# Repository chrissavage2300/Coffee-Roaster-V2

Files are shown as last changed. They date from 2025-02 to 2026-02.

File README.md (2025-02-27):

# Coffee-Roaster-V2
My Second DIY coffee roaster

Parts not listed on BOM:

Intake fan: BL4447-04W-B49

https://www.aliexpress.us/item/2251800670595894.html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

Exhaust fan: 4090D 12V

https://www.aliexpress.us/item/3256805403626998.html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

SSR: GSR1-1-25DA

https://www.aliexpress.us/item/3256802111187964.html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

Gears for drum: 1M40T-Bore 6 mm

https://www.aliexpress.us/item/2255800052157775.html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

Drum Motor: 12V Single Motor, 66RPM

https://www.aliexpress.us/item/3256805242242724.html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

K type thermocouples:

https://finglai.aliexpress.com/store/1100819105?spm=a2g0o.order_list.order_list_main.187.4b841802Pr1vyz

Knobs:

https://www.aliexpress.us/item/3256807011356288.html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

LCD

https://www.aliexpress.us/item/2251832723901253.html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

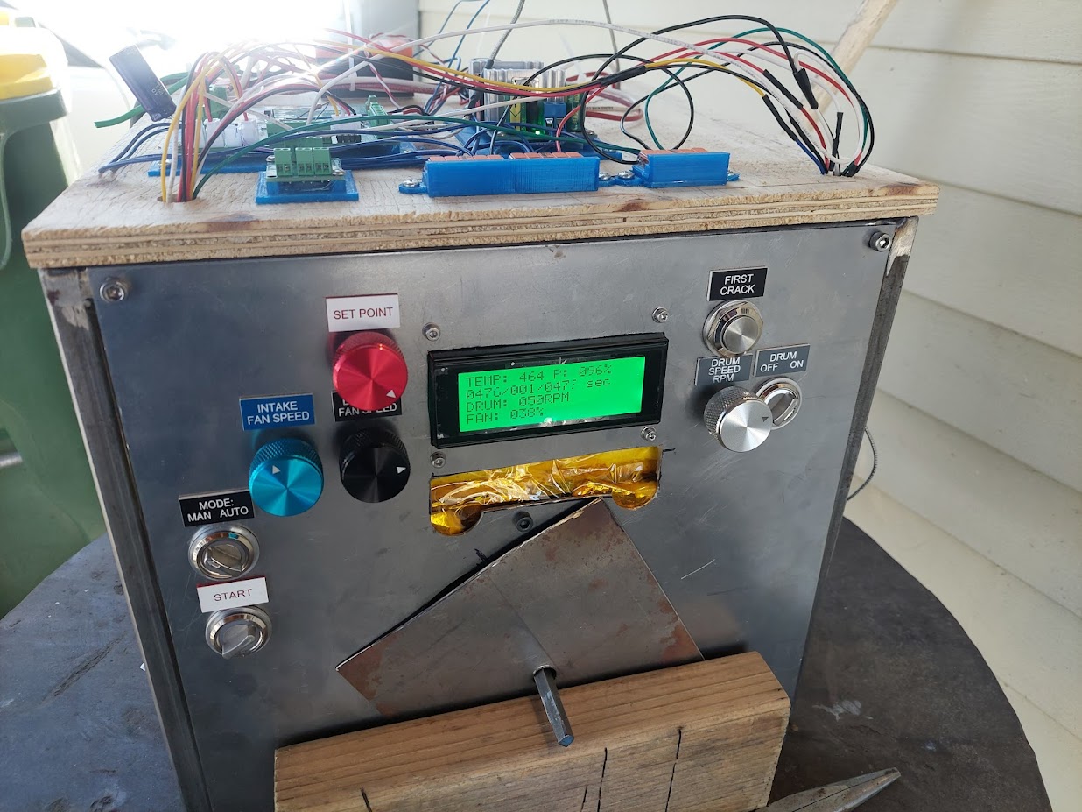
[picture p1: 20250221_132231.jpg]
roaster


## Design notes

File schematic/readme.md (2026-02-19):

I used Eagle PCB. I will convert further versions to KiCad

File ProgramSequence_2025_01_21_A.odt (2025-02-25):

Two Modes of operation via a selector switch that toggles each mode:
Green is to do

Manual Mode: □

- Set Point Pot will set the amount of power from 0 to 100%□
- in code this will be 0 to 31000 increments that determine how much power gets passed to the heater. This turns the auto mode off. This mode uses Output compare module #3□
- There will be an over temp set in the program of 470 degrees. This is for the feedback temperature, not the set point.
- Over temp condition will shut off the heater. Start LED will blink.
- ~~A Blue LED will come on~~ No LED

Auto mode (not implemented) □

- Will perform a PI function to control the heater based on the set point set via a pot.
- PI code will adjust heater until its up to temp. This turns off manual mode.
- A Blue LED will come on.

In both modes:

Intake and exhaust fans are DC PWM control and come in when start button is on. Exhaust fan not implemented yet.

- Display 0-100%□
- Fans will be OFF when start button is OFF. □
- Start LED will come on□

Drum Speed has on and off latched switch

- Display 0 to 66 RPM (0 to 100% Duty) □

Start mode is a latched switch. This starts either mode. Switching it off will stop the machine ~~and reset any counters~~

-Addendum: Timer can be reset with start mode off and FC pressed. □

First Crack push button sets the current time to 0 and displays the time at which the button was pressed. □

- 1 second timer counts up until user hits FC button. This will use the INT0 interrupt pin to count up to 120, which is one second. We use the INT0 pin because line frequency might be more accurate. □
- NOTE: FRC is accurate to +/-3%. 1 Second time means 1.03 to 0.98 seconds. Over 10 minutes this is +/-18 seconds.
- Screen will be updated during this time. □
- I2C ADC will also be read during this time □

ADC algorithm will perform calculation on K-type thermocouple using linearization based on voltage.

Formula for final thermocouple is as follows: first the MCP9800 must be read, this gives the temperature in a digital format. Then the temperature must be converted back into a voltage via a linear formula. The onboard temp sensor should only see temperatures up to 40C, so the formula only goes up this far. I’ll call this VCJC, or Voltage Cold Junction Comp. □

Then the thermocouple voltage will be read. This voltage, called Vtc (thermocouple voltage) will then be added to Vcjc. The final voltage will be entered into an equation to solve for the temperature.

□20 Minute Burn in test without heat

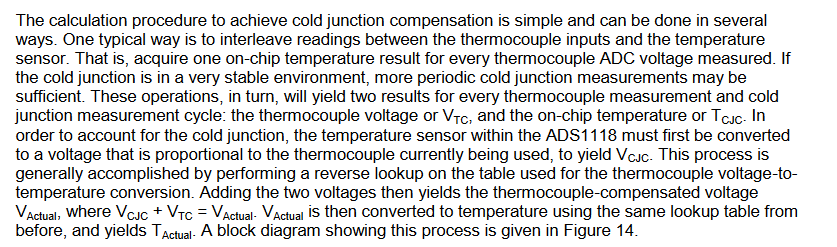
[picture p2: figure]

□20 minute burn in test with heat

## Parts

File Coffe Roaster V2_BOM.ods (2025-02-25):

Part | Value | Device | Package | Description
12V | M025MM | M025MM | SCREWTERMINAL-5MM-2 | Standard 2-pin 0.1" header. Use with
120VACOUT | M025MM | M025MM | SCREWTERMINAL-5MM-2 | Standard 2-pin 0.1" header. Use with
C1 | 0.1uF | CAP0805 | 805 | Capacitor
C2 | 0.1uF | CAP0805 | 805 | Capacitor
C3 | 0.1uF | CAP0805 | 805 | Capacitor
C4 | 0.1uF | CAP0805 | 805 | Capacitor
C5 | 0.1u | CAP1206 | 1206 | Capacitor
C6 | 0.1u | CAP1206 | 1206 | Capacitor
C7 | 0.1u | CAP1206 | 1206 | Capacitor
C8 | 0.1uF | CAP0805 | 805 | Capacitor
C9 | 0.1uF | CAP0805 | 805 | Capacitor
C10 | 0.1uF | CAP0805 | 805 | Capacitor
C11 | 0.1uF | CAP0805 | 805 | Capacitor
C12 | 0.1uF | CAP0805 | 805 | Capacitor
C13 | 0.1uF | CAP0805 | 805 | Capacitor
DRUM |  | M03POLAR_LOCK | MOLEX-1X3_LOCK | Header 3
EXT |  | M03POLAR_LOCK | MOLEX-1X3_LOCK | Header 3
F1 | 16A | FUSE | FUSE | FUSE
FAN | M02POLAR_LOCK | M02POLAR_LOCK | MOLEX-1X2_LOCK | Standard 2-pin 0.1" header. Use with
I2C2 | I2C5V | M04JST | 1X04-1.5MM_JST | Header 4
IC1 | AZ1117C | ADP3338AKCZ-5-R7 | SOT230P700X180-4N | Low Dropout Regulator
IC2 | AZ1117CR-3.3TRG1 | AZ1117CR-3.3TRG1 | SOT89_AZ1117_DIO
IC4 | MCP9801-M/SNSOIC8-N_MC_MCH-M | MCP9801-M/SNSOIC8-N_MC_MCH-M | SOIC8-N_MC_MCH-M
IC5 | MCP3424-E/SLSOIC14-N_MC_MCH-M | MCP3424-E/SLSOIC14-N_MC_MCH-M | SOIC14-N_MC_MCH-M | Analog to Digital Converters - ADC 18B delta-sigma ADC dual Ch 4sps
INT |  | M03POLAR_LOCK | MOLEX-1X3_LOCK | Header 3
ISO1 | MOC3021SMOC3021S_LTO-M | MOC3021SMOC3021S_LTO-M | MOC3021S_LTO-M
ISO2 | LTV-814S-TA1 | SFH6206 | DIL4-SMD | Optocoupler, Phototransistor Output, AC Input
J2 | EXPANSION | M04JST | 1X04-1.5MM_JST | Header 4
JP1 | ICSP | M05PTH | 1X05 | Header 5
JP2 |  | M02POLAR_LOCK | MOLEX-1X2_LOCK | Header 2
JP3 |  | M02POLAR_LOCK | MOLEX-1X2_LOCK | Header 2
JP4 | M01PTH | M01PTH | 1X01 | Header 1
JP5 | UART | M04LOCK | 1X04_LOCK | Header 4
JP6 |  | M083.5MM-8 | SCREWTERMINAL-3.5MM-8 | Header 8
JP7 |  | M02POLAR_LOCK | MOLEX-1X2_LOCK | Header 2
JP8 |  | M04LOCK_LONGPADS | 1X04_LOCK_LONGPADS | Header 4
JP10 | M10LOCK_LONGPADS | M10LOCK_LONGPADS | 1X10_LOCK_LONGPADS | Header 10
JP11 | M01PTH | M01PTH | 1X01 | Header 1
LED1 | GRN | LED1206 | LED-1206 | LEDs
LED2 | YELLOW | LED1206 | LED-1206 | LEDs
LED3 | GRN | LED1206 | LED-1206 | LEDs
LED4 | YELLOW | LED1206 | LED-1206 | LEDs
LED5 | BLUE | LED1206 | LED-1206 | LEDs
LED6 | BLUE | LED1206 | LED-1206 | LEDs
PIN | M025MM | M025MM | SCREWTERMINAL-5MM-2 | Standard 2-pin 0.1" header. Use with
POUT | M025MM | M025MM | SCREWTERMINAL-5MM-2 | Standard 2-pin 0.1" header. Use with
Q1 | DMN3032LE-13 | NFET_SOT_223 | SOT223
Q2 | DMN3032LE-13 | NFET_SOT_223 | SOT223
Q3 | DMN3032LE-13 | NFET_SOT_223 | SOT223
R1 | 200 | R-US_R2512 | R2512 | RESISTOR, American symbol
R2 | 15k | R-US_R2512 | R2512 | RESISTOR, American symbol
R3 | 15k | R-US_R2512 | R2512 | RESISTOR, American symbol
R4 | 220 | RESISTOR1206 | 1206 | Resistor
R5 | 2k | RESISTOR1206 | 1206 | Resistor
R6 | 340 | RESISTOR1206 | 1206 | Resistor
R7 | 2k | RESISTOR1206 | 1206 | Resistor
R8 | 10k | R-US_M0805 | M0805 | RESISTOR, American symbol
R9 | 10k | R-US_M0805 | M0805 | RESISTOR, American symbol
R10 | 340 | RESISTOR1206 | 1206 | Resistor
R11 | 2k | RESISTOR1206 | 1206 | Resistor
R12 | 2k | RESISTOR1206 | 1206 | Resistor
R15 | 2k | RESISTOR1206 | 1206 | Resistor
R16 | 2k | RESISTOR1206 | 1206 | Resistor
R19 | 340 | RESISTOR1206 | 1206 | Resistor
R20 | 100k | RESISTOR1206 | 1206 | Resistor
SP |  | M03POLAR_LOCK | MOLEX-1X3_LOCK | Header 3
T1 | BT138-600,127 | BT138-V | TO220BV | TRIAC
U2 | DSPIC33EP32MC204-I/PTTQFP44_10X10MC_MCH-M | DSPIC33EP32MC204-I/PTTQFP44_10X10MC_MCH-M | TQFP44_10X10MC_MCH-M

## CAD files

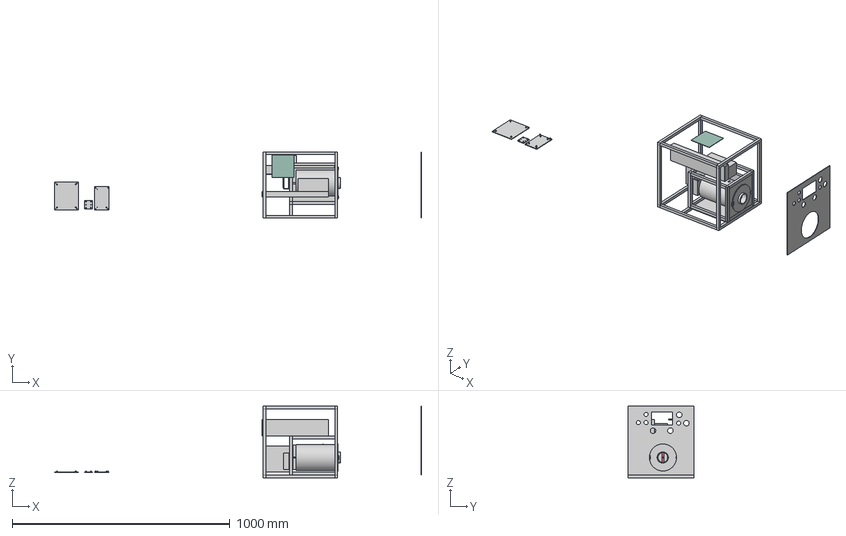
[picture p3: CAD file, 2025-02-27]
3D CAD/Coffee Roaster V2.0 v107.step
1686.0 x 304.8 x 330.2 mm
Make This Part (1)
Drum (1)
End Cap (Cut) (1)
1800W Heater
FAN (1)
bushing2
Motor Holder
FL
FrontLeft (1)
BL
TL
1603A2_Surface-Mount Hinge with Holes
4x4PCB

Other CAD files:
3D CAD/Coffee Roaster V2.0 v107.f3d

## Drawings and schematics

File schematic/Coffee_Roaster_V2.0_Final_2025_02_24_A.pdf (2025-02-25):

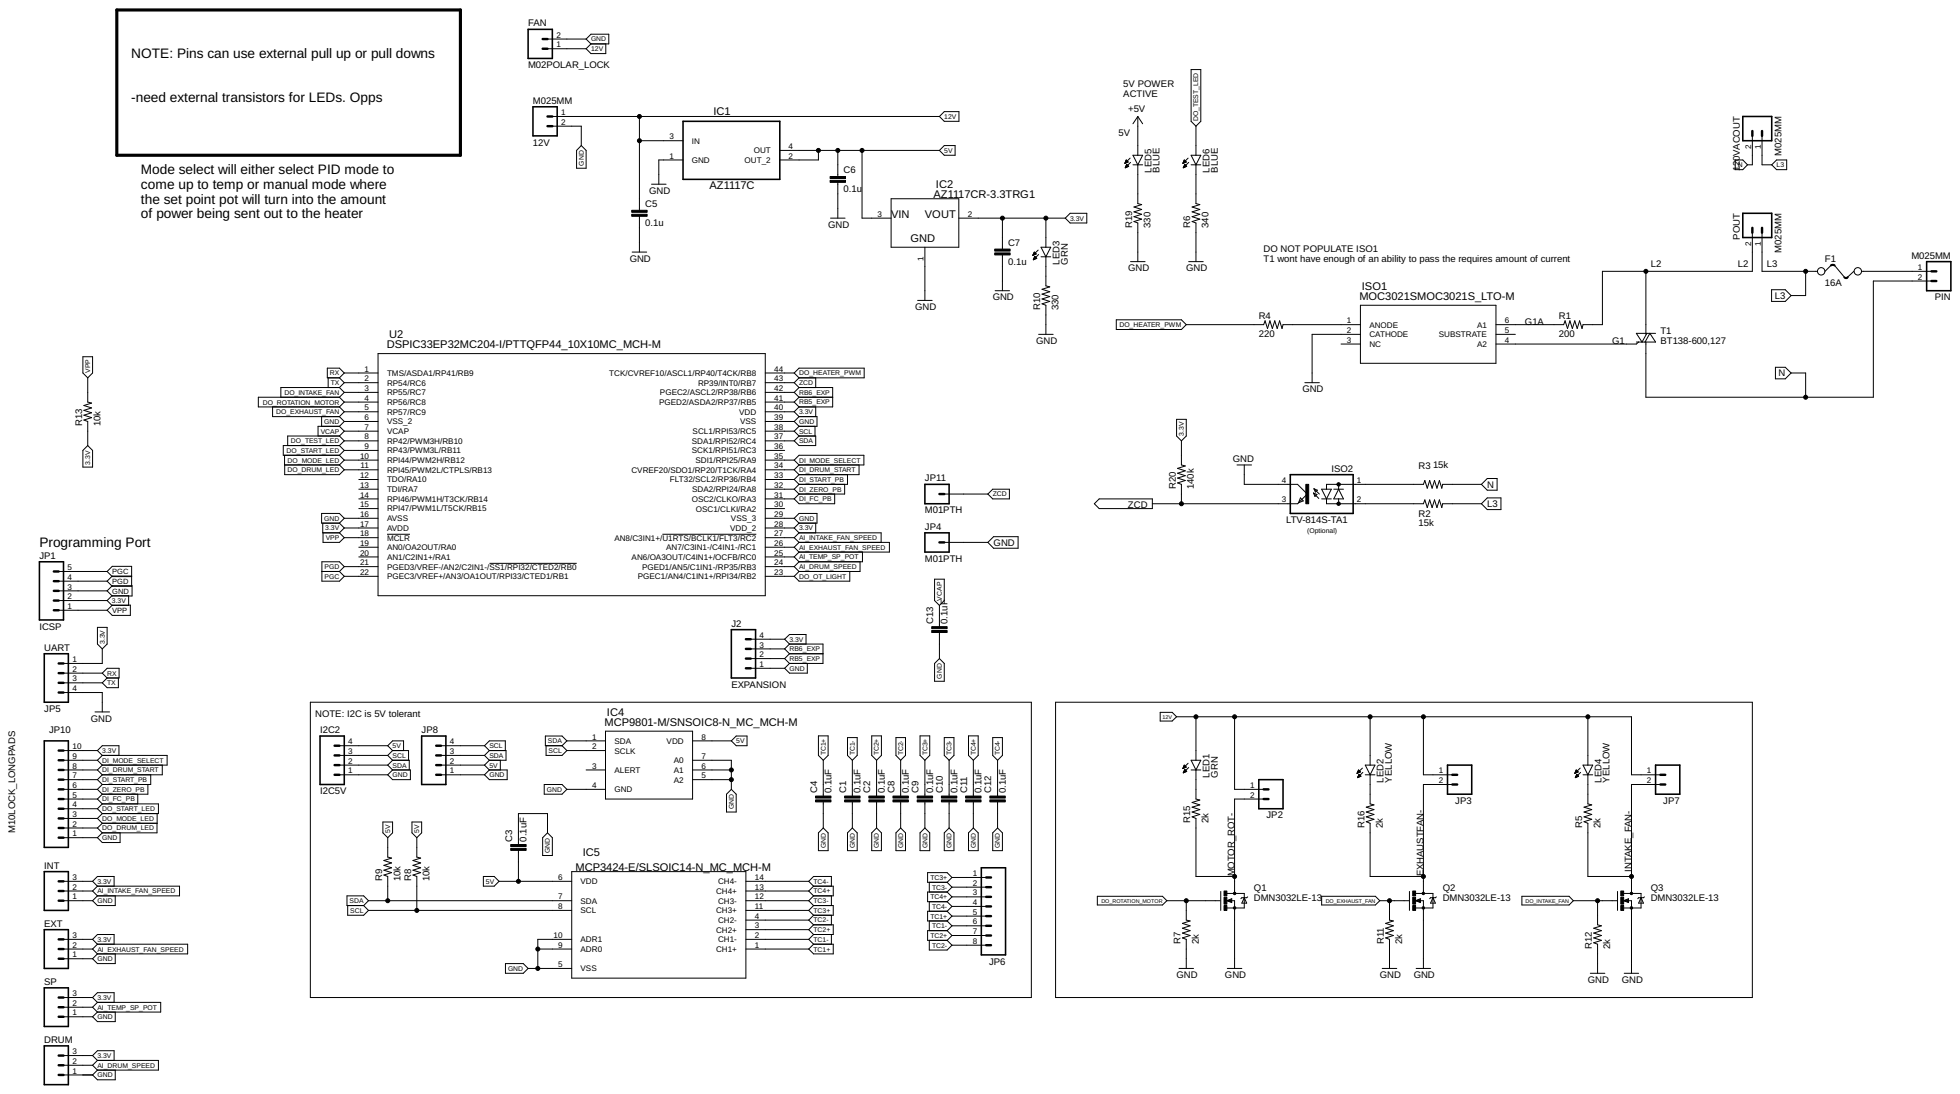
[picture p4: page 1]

ACTIVE NOTE: Pins can use external pull up or pull downs

-need external transistors for LEDs. Opps Mode select will either select PID mode to

come up to temp or manual mode where

GND GND GND GND

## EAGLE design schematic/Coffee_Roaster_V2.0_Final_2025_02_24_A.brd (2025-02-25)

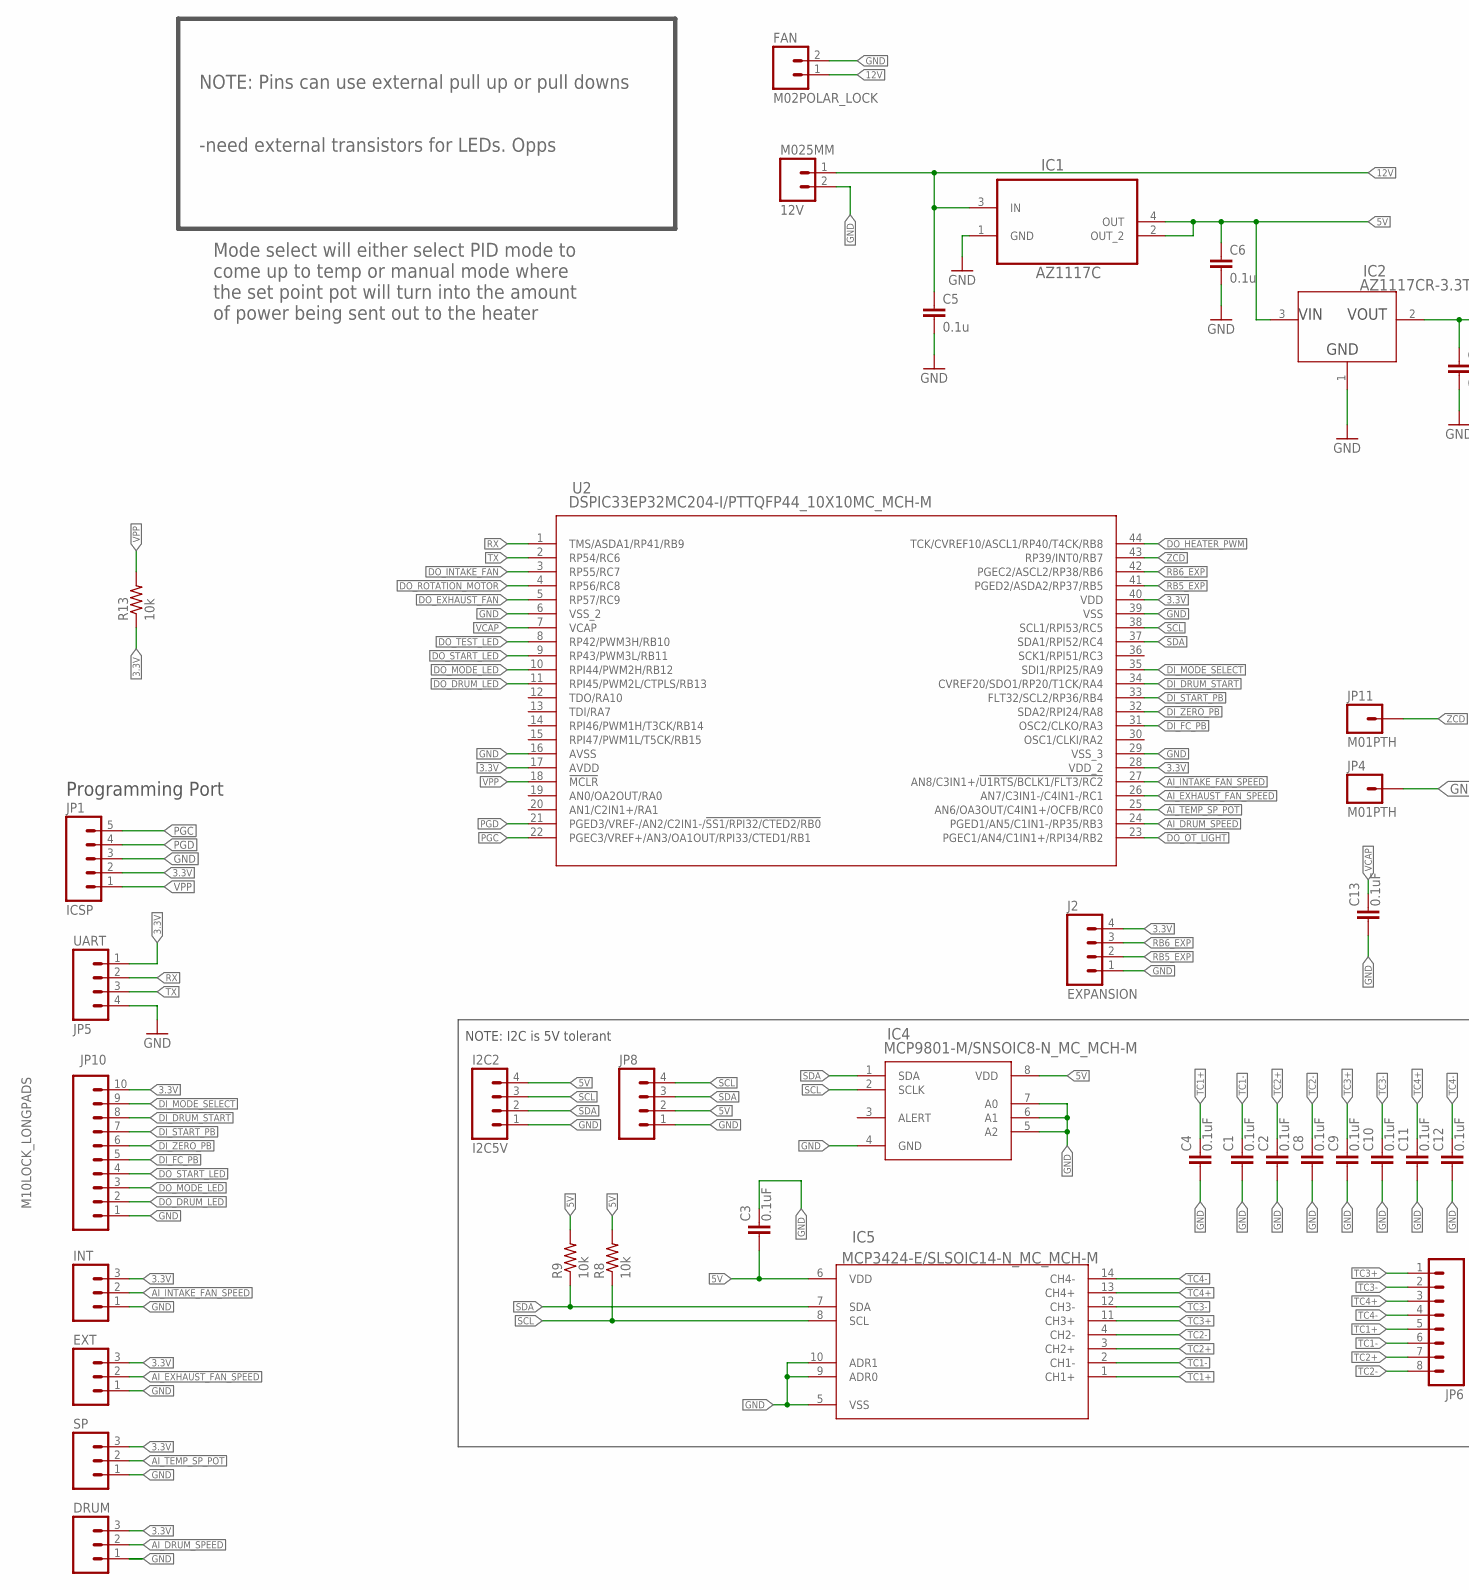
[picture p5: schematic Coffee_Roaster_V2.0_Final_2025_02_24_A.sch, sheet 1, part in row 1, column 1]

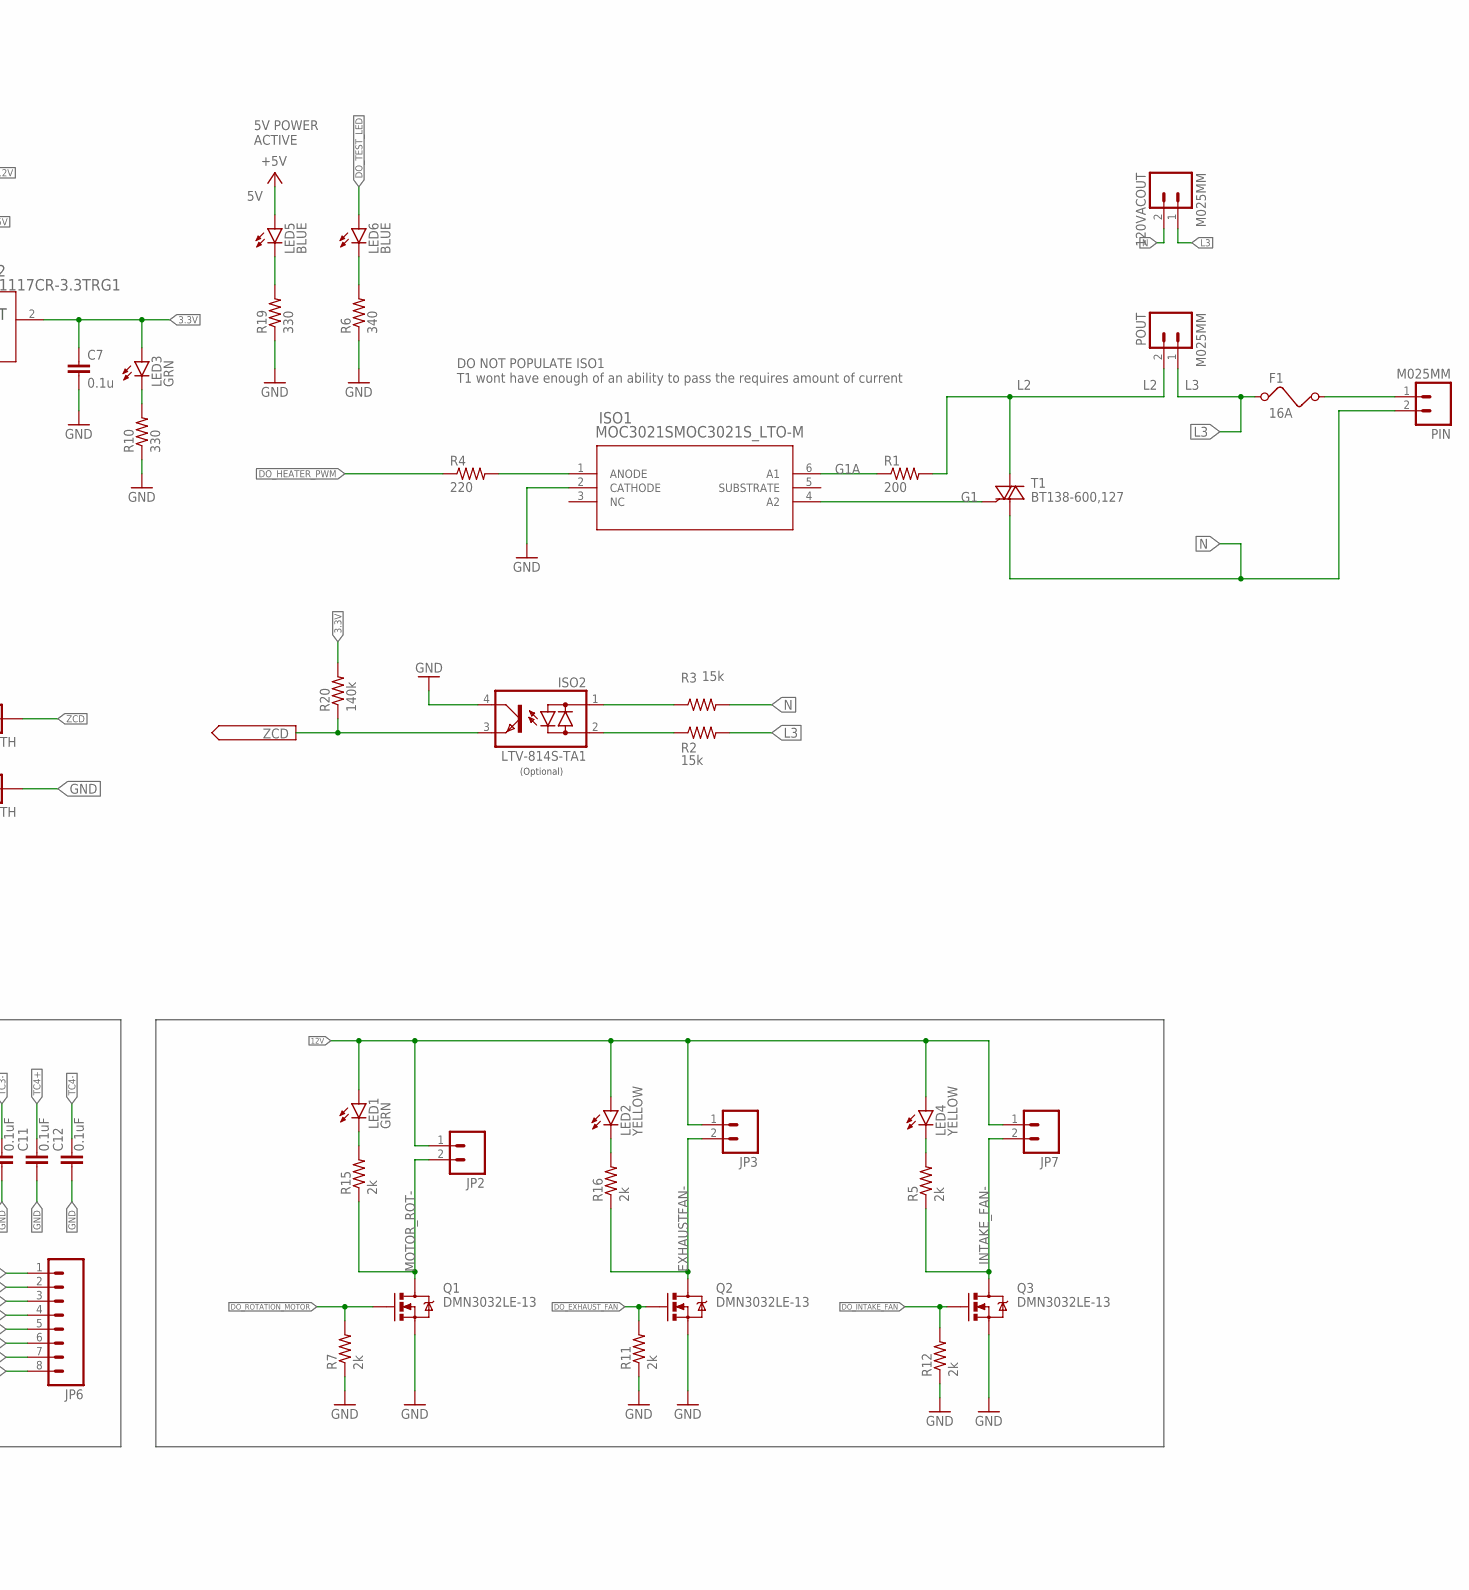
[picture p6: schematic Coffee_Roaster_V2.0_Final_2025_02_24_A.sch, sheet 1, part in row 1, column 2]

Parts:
12V, 120VACOUT: M025MM; SCREWTERMINAL-5MM-2
C1, C2, C3, C4, C8, C9, C10, C11, C12, C13: 0.1uF; 0805
C5, C6, C7: 0.1u; 1206
DRUM: M03POLAR_LOCK; MOLEX-1X3_LOCK
EXT: M03POLAR_LOCK; MOLEX-1X3_LOCK
F1: 16A; FUSE
FAN: M02POLAR_LOCK; MOLEX-1X2_LOCK
I2C2: I2C5V; 1X04-1.5MM_JST
IC1: AZ1117C; SOT230P700X180-4N
IC2: AZ1117CR-3.3TRG1; SOT89_AZ1117_DIO
IC4: MCP9801-M/SNSOIC8-N_MC_MCH-M; SOIC8-N_MC_MCH-M
IC5: MCP3424-E/SLSOIC14-N_MC_MCH-M; SOIC14-N_MC_MCH-M
INT: M03POLAR_LOCK; MOLEX-1X3_LOCK
ISO1: MOC3021SMOC3021S_LTO-M; MOC3021S_LTO-M
ISO2: LTV-814S-TA1; DIL4-SMD
J2: EXPANSION; 1X04-1.5MM_JST
JP1: ICSP; 1X05
JP2, JP3, JP7: M02POLAR_LOCK; MOLEX-1X2_LOCK
JP4, JP11: M01PTH; 1X01
JP5: UART; 1X04_LOCK
JP6: M083.5MM-8; SCREWTERMINAL-3.5MM-8
JP8: M04LOCK_LONGPADS; 1X04_LOCK_LONGPADS
JP10: M10LOCK_LONGPADS; 1X10_LOCK_LONGPADS
LED1, LED3: GRN; LED-1206
LED2, LED4: YELLOW; LED-1206
LED5, LED6: BLUE; LED-1206
PIN: M025MM; SCREWTERMINAL-5MM-2
POUT: M025MM; SCREWTERMINAL-5MM-2
Q1, Q2, Q3: DMN3032LE-13; SOT223
R1: 200; R2512
R2, R3: 15k; R2512
R4: 220; 1206
R5, R7, R11, R12, R15, R16: 2k; 1206
R6: 340; 1206
R8, R9, R13: 10k; M0805
R10, R19: 330; 1206
R20: 140k; 1206
SP: M03POLAR_LOCK; MOLEX-1X3_LOCK
T1: BT138-600,127; TO220BV
U2: DSPIC33EP32MC204-I/PTTQFP44_10X10MC_MCH-M; TQFP44_10X10MC_MCH-M

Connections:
3.3V: C7.1, DRUM.3, EXT.3, IC2.2 (OUTPUT), INT.3, J2.4, JP1.2, JP5.1, JP10.10, LED3.A, R13.1, R20.2, SP.3, U2.17 (AVDD), U2.28 (VDD_2), U2.40 (VDD)
5V: C3.1, C6.1, I2C2.4, IC1.2 (OUT_2), IC1.4 (OUT), IC2.3 (INPUT), IC4.8 (VDD), IC5.6 (VDD), JP8.2, LED5.A, R8.2, R9.2
12V: 12V.1, C5.1, FAN.1, IC1.3 (IN), JP2.1, JP3.1, JP7.1, LED1.A, LED2.A, LED4.A
AI_DRUM_SPEED: DRUM.2, U2.24 (PGED1/AN5/C1IN1-/RP35/RB3)
AI_EXHAUST_FAN_SPEED: EXT.2, U2.26 (AN7/C3IN1-/C4IN1-/RC1)
AI_INTAKE_FAN_SPEED: INT.2, U2.27 (AN8/C3IN1+/!U1RTS/BCLK1/FLT3/RC2)
AI_TEMP_SP_POT: SP.2, U2.25 (AN6/OA3OUT/C4IN1+/OCFB/RC0)
DI_DRUM_START: JP10.8, U2.34 (CVREF20/SDO1/RP20/T1CK/RA4)
DI_FC_PB: JP10.5, U2.31 (OSC2/CLKO/RA3)
DI_MODE_SELECT: JP10.9, U2.35 (SDI1/RPI25/RA9)
DI_START_PB: JP10.7, U2.33 (FLT32/SCL2/RP36/RB4)
DI_ZERO_PB: JP10.6, U2.32 (SDA2/RPI24/RA8)
DO_DRUM_LED: JP10.2, U2.11 (RPI45/PWM2L/CTPLS/RB13)
DO_EXHAUST_FAN: Q2.1 (G), R11.2, U2.5 (RP57/RC9)
DO_HEATER_PWM: R4.1, U2.44 (TCK/CVREF10/ASCL1/RP40/T4CK/RB8)
DO_INTAKE_FAN: Q3.1 (G), R12.2, U2.3 (RP55/RC7)
DO_MODE_LED: JP10.3, U2.10 (RPI44/PWM2H/RB12)
DO_OT_LIGHT: U2.23 (PGEC1/AN4/C1IN1+/RPI34/RB2)
DO_ROTATION_MOTOR: Q1.1 (G), R7.2, U2.4 (RP56/RC8)
DO_START_LED: JP10.4, U2.9 (RP43/PWM3L/RB11)
DO_TEST_LED: LED6.A, U2.8 (RP42/PWM3H/RB10)
EXHAUSTFAN-: JP3.2, Q2.2 (D), Q2.4 (D), R16.1
G1: ISO1.4 (A2), T1.G
G1A: ISO1.6 (A1), R1.1
GND: 12V.2, C1.1, C2.1, C3.2, C4.1, C5.2, C6.2, C7.2, C8.1, C9.1, C10.1, C11.1, C12.1, C13.1, DRUM.1, EXT.1, FAN.2, I2C2.1, IC1.1 (GND), IC2.1 (ADJ/GND), IC4.4 (GND), IC4.5 (A2), IC4.6 (A1), IC4.7 (A0), IC5.5 (VSS), IC5.9 (ADR0), IC5.10 (ADR1), INT.1, ISO1.2 (CATHODE), ISO2.4 (C), J2.1, JP1.3, JP4.1, JP5.4, JP8.1, JP10.1, Q1.3 (S), Q2.3 (S), Q3.3 (S), R6.1, R7.1, R10.1, R11.1, R12.1, R19.1, SP.1, U2.6 (VSS_2), U2.16 (AVSS), U2.29 (VSS_3), U2.39 (VSS)
INTAKE_FAN-: JP7.2, Q3.2 (D), Q3.4 (D), R5.1
L1: F1.2, PIN.1
L2: POUT.2, R1.2, T1.T2 (A2)
L3: 120VACOUT.1, F1.1, POUT.1, R2.2
MOTOR_ROT-: JP2.2, Q1.2 (D), Q1.4 (D), R15.1
N: 120VACOUT.2, PIN.2, R3.2, T1.T1 (A1)
unnamed: ISO1.1 (ANODE), R4.2
unnamed: LED3.C, R10.2
unnamed: LED1.C, R15.2
unnamed: LED2.C, R16.2
unnamed: ISO2.1 (AC1), R3.1
unnamed: ISO2.2 (AC2), R2.1
unnamed: LED4.C, R5.2
unnamed: LED6.C, R6.2
unnamed: LED5.C, R19.2
PGC: JP1.5, U2.22 (PGEC3/VREF+/AN3/OA1OUT/RPI33/CTED1/RB1)
PGD: JP1.4, U2.21 (PGED3/VREF-/AN2/C2IN1-/!SS1/RPI32/CTED2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)
RB5_EXP: J2.2, U2.41 (PGED2/ASDA2/RP37/RB5)
RB6_EXP: J2.3, U2.42 (PGEC2/ASCL2/RP38/RB6)
RX: JP5.2, U2.1 (TMS/ASDA1/RP41/RB9)
SCL: I2C2.3, IC4.2 (SCLK), IC5.8 (SCL), JP8.4, R8.1, U2.38 (SCL1/RPI53/RC5)
SDA: I2C2.2, IC4.1 (SDA), IC5.7 (SDA), JP8.3, R9.1, U2.37 (SDA1/RPI52/RC4)
TC1+: C4.2, IC5.1 (CH1+), JP6.5
TC1-: C1.2, IC5.2 (CH1-), JP6.6
TC2+: C2.2, IC5.3 (CH2+), JP6.7
TC2-: C8.2, IC5.4 (CH2-), JP6.8
TC3+: C9.2, IC5.11 (CH3+), JP6.1
TC3-: C10.2, IC5.12 (CH3-), JP6.2
TC4+: C11.2, IC5.13 (CH4+), JP6.3
TC4-: C12.2, IC5.14 (CH4-), JP6.4
TX: JP5.3, U2.2 (RP54/RC6)
VCAP: C13.2, U2.7 (VCAP)
VPP: JP1.1, R13.2, U2.18 (!MCLR)
ZCD: ISO2.3 (E), JP11.1, R20.1, U2.43 (RP39/INT0/RB7)

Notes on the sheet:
Programming Port
5V POWER ACTIVE
(Optional)
NOTE: Pins can use external pull up or pull downs -need external transistors for LEDs. Opps
NOTE: I2C is 5V tolerant
Mode select will either select PID mode to come up to temp or manual mode where the set point pot will turn into the amount of power being sent out to the heater
DO NOT POPULATE ISO1 T1 wont have enough of an ability to pass the requires amount of current

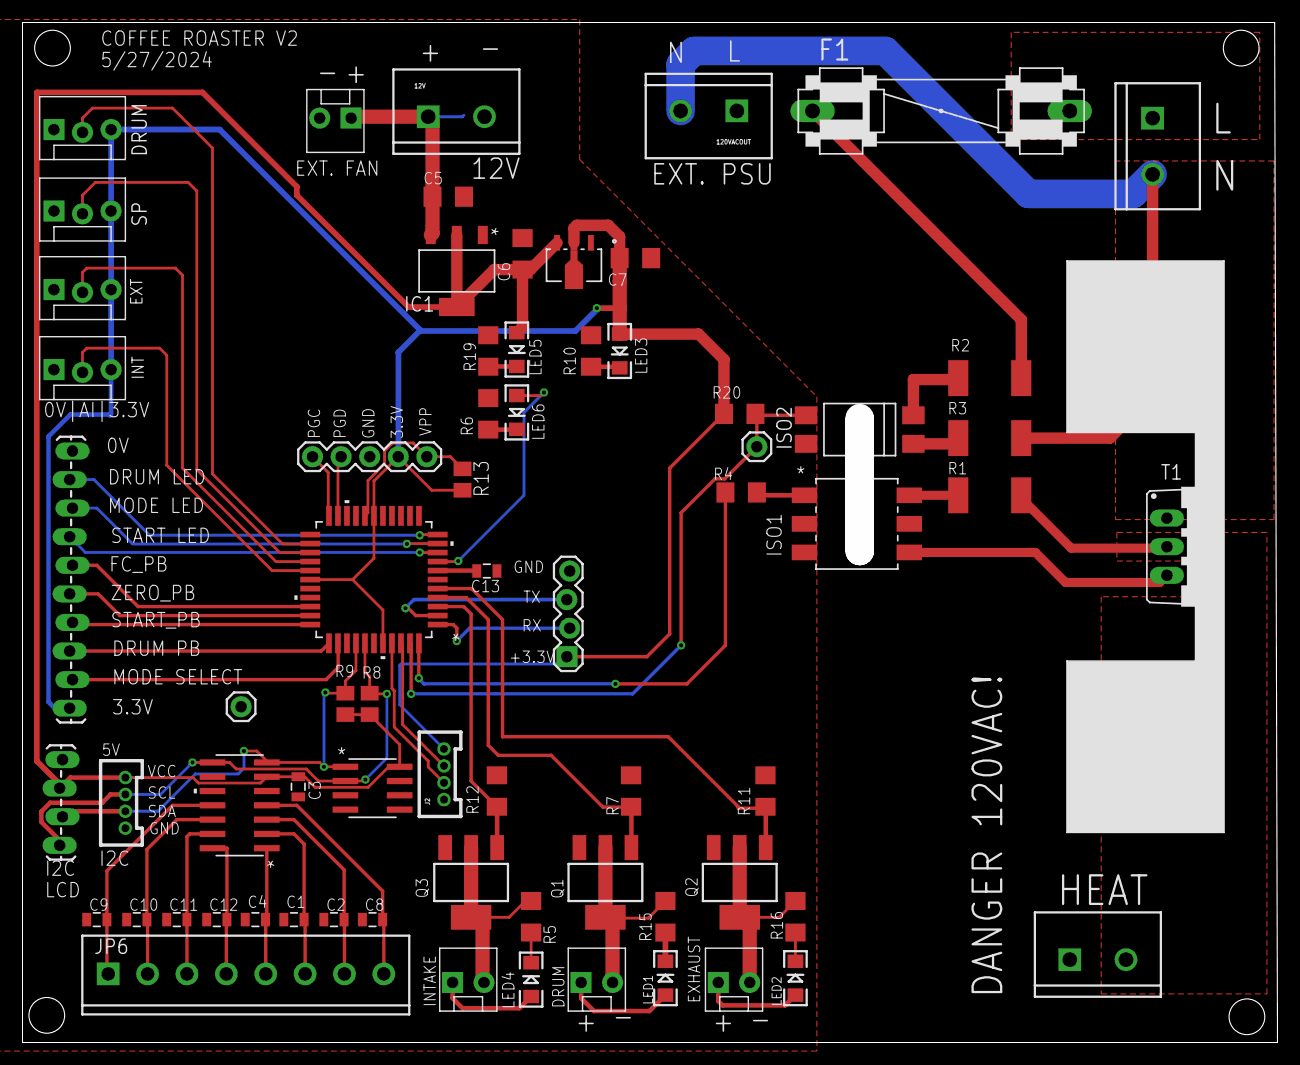
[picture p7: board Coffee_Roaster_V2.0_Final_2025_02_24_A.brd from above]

Board: 2 copper layers, 111.6 x 90.7 mm, 70 parts (0 on the bottom side), 58 nets.

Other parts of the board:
HEATSINK: 7-345-2PP-BA

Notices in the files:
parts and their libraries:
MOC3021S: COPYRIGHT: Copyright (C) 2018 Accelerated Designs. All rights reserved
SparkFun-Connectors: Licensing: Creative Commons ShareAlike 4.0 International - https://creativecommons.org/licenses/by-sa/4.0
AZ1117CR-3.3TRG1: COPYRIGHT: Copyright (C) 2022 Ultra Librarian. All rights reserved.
